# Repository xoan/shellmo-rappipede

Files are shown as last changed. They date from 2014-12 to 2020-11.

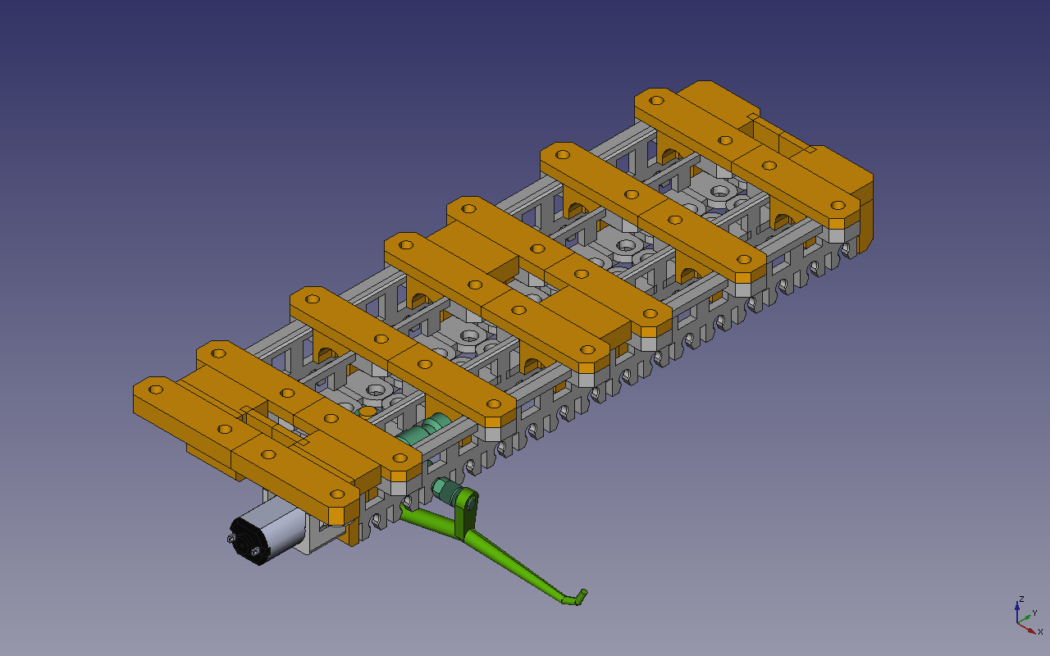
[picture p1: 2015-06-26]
images/chassis.png

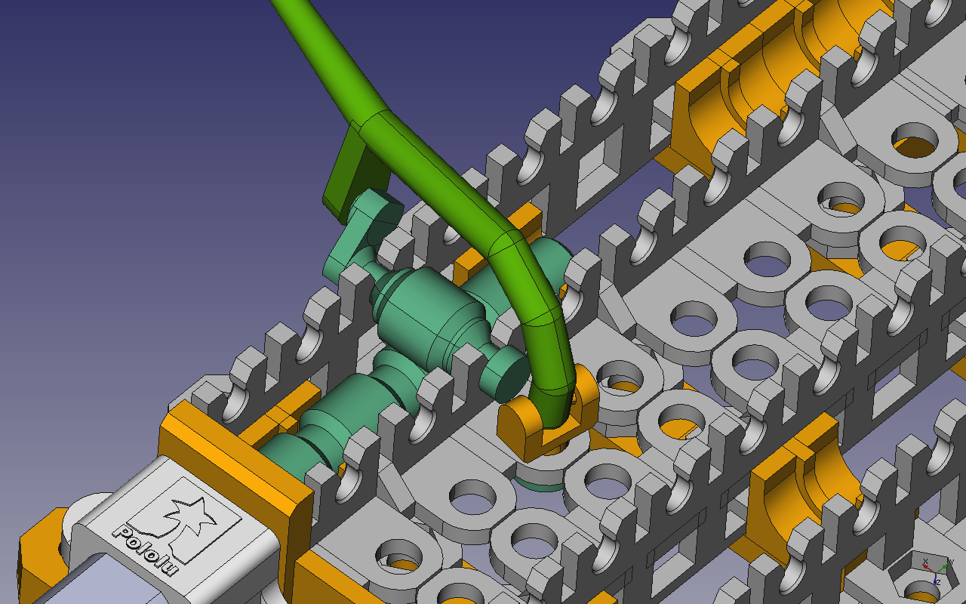
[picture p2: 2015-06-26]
images/leg-pin.png

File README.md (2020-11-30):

# Rappipede for Shellmo

RepRap printable version of [Micropede][mpdoc] motor module for [Shellmo][spweb].

[mpdoc]: http://shellmo.org/making-micropede.html
[spweb]: http://shellmo.org/

## Printing

All the parts can be printed without support.

Recommended settings for Slic3r 1.2.1:

* layer height: 0.25mm
* infill: 30%
* extrusion width: 0.5mm

## Assembly ([in pictures][mpagp])

* M3x8mm screw **x24**
* M3x10mm screw **x4** (for motor cover)
* M3 nut **x28**

Please, refer to `src/chassis.fcstd` to see the pin-leg connection and to
figure out how to assembly the whole thing. You must put all the pins before
to assembly the ribs, and also before this you must put the captive nuts.

Shaft is a tricky part. Try to fit all the shaft parts without glue and
without play, and insert in the ribs before put the rear one.

The rest is the same in [Micropede documentation][mpdoc].

The compatible motor cover is the one you can find in the [RepWalker][rwdoc].

[mpagp]: https://photos.app.goo.gl/5GXLVykhWVXsJaY36
[rwdoc]: http://shellmo.org/making-repwalker.html

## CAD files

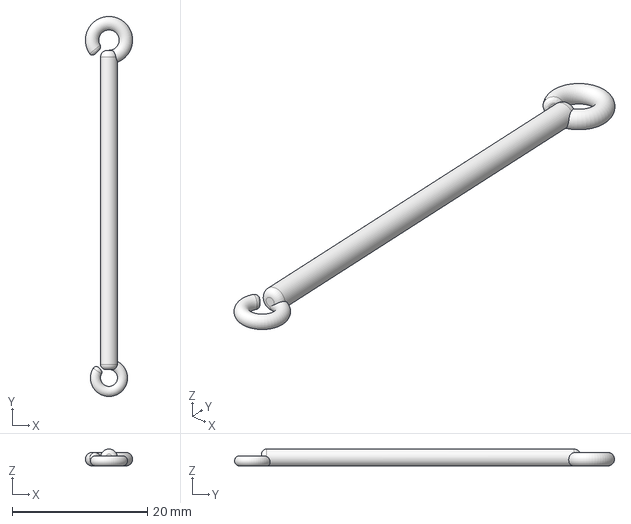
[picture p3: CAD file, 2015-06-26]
src/linkrod.fcstd
7.00 x 56.2 x 2.50 mm

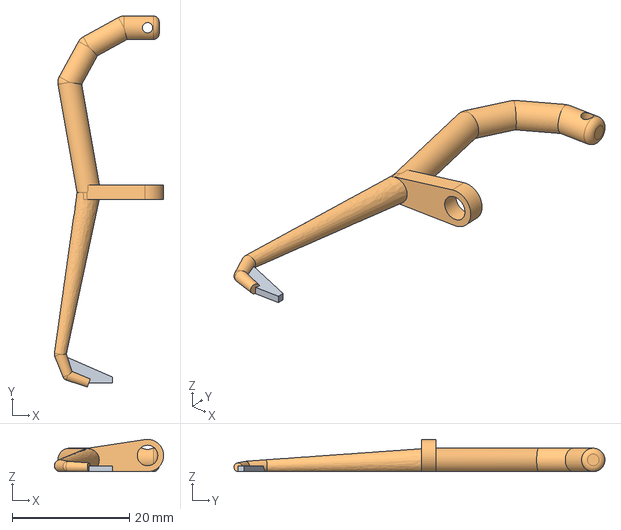
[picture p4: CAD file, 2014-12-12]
step/leg.step
18.6 x 63.2 x 5.50 mm

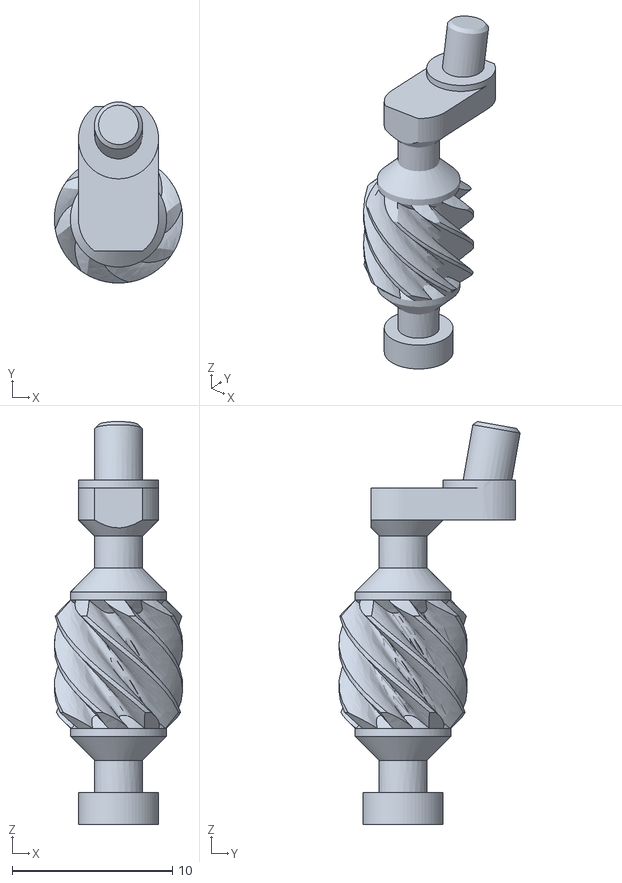
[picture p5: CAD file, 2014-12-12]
stl/ns/crank-RNS.stl
8.00 x 11.3 x 25.1

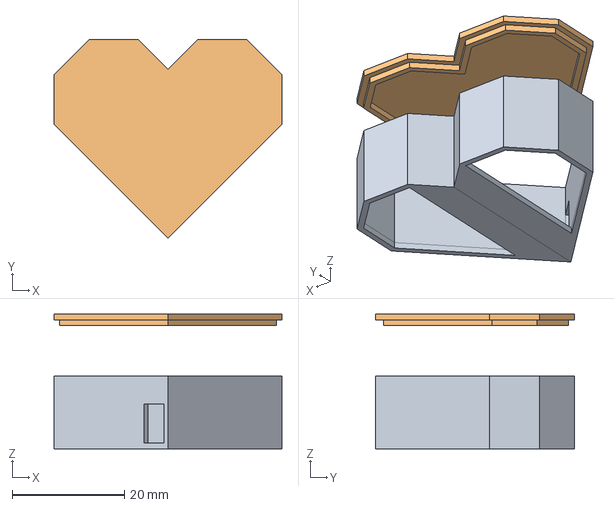
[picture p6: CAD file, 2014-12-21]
src/heart.fcstd
40.6 x 35.4 x 24.0 mm

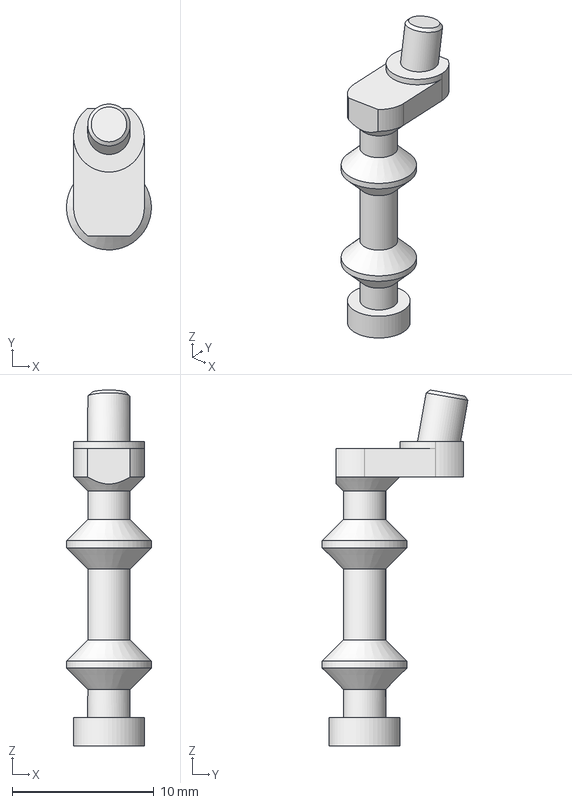
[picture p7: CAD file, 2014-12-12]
step/crank-axis.step
5.99 x 10.3 x 25.1 mm

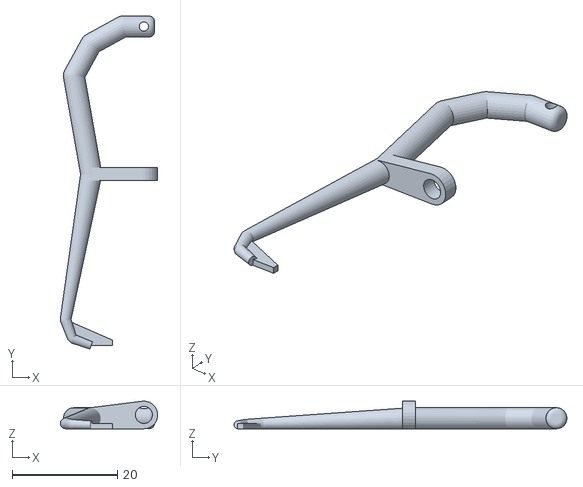
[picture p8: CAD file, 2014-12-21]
stl/leg-L_x16.stl
18.5 x 63.2 x 5.23

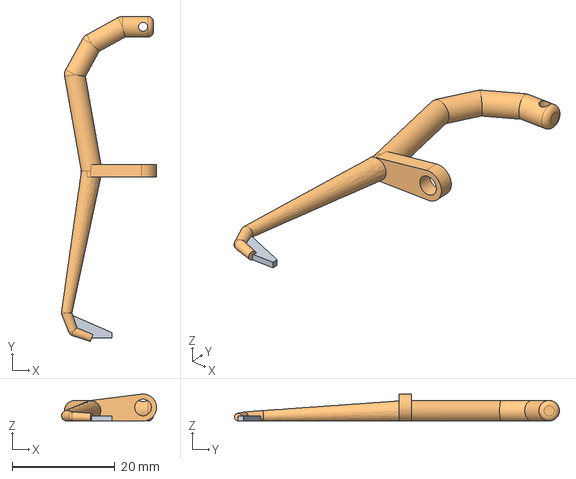
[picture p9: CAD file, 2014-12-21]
src/leg.fcstd
18.5 x 63.2 x 5.25 mm
foot-Pad001
leg-Fillet

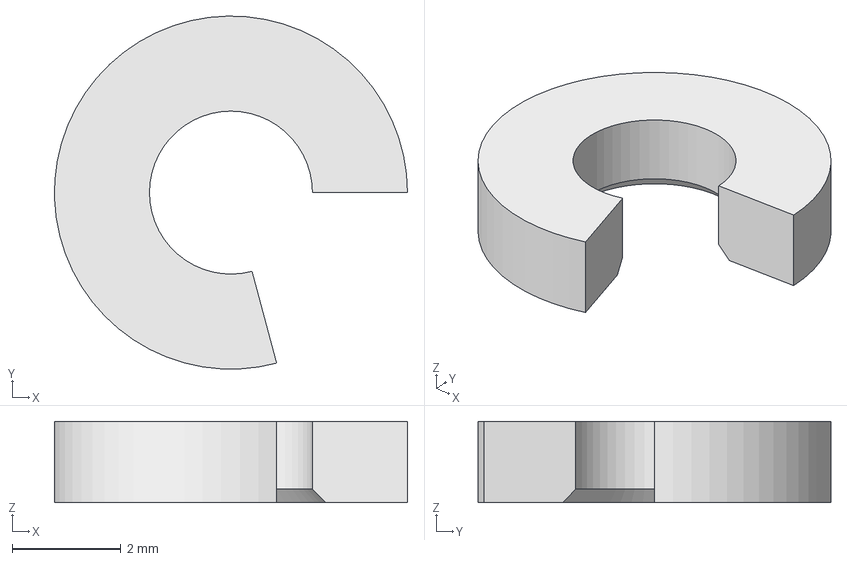
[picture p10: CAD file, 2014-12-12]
step/cring.step
6.50 x 6.50 x 1.50 mm

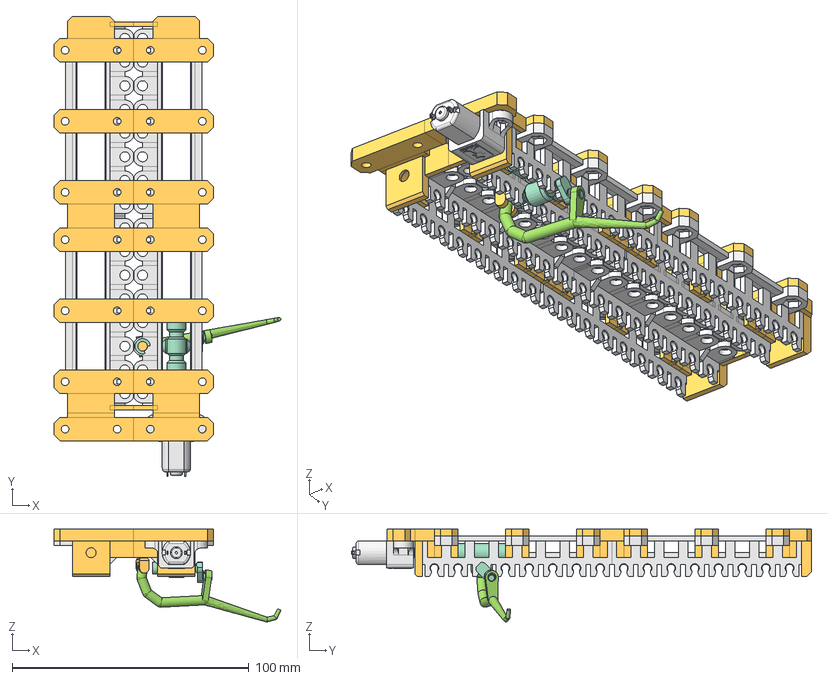
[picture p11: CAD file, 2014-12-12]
src/chasis.fcstd
95.8 x 194.2 x 39.2 mm
crank-Fusion-Clone009
shaft-Fusion009
motor-Part__Feature001
pin-Part__Feature002
leg-Part__Feature004
cring-Part__Feature005
outside-Compound
inside-Compound001
outside-Part__Mirroring004
inside-Part__Mirroring005
rib-Fusion019-Clone002
rib-Fusion019-Clone003
rib-union-Fusion021
rib-rear-Chamfer010
rib-front-Fusion025

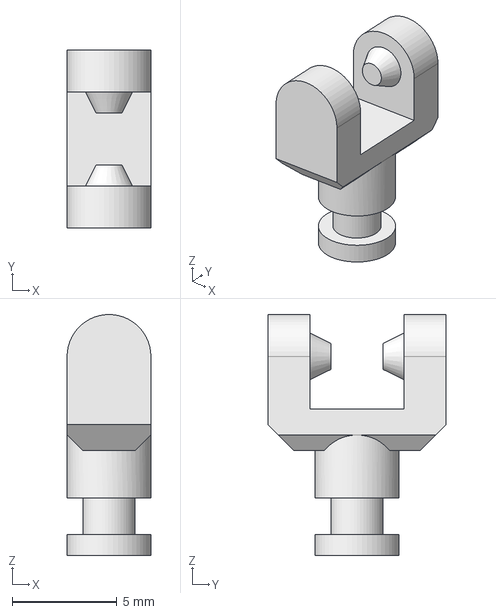
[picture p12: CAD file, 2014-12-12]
step/pin.step
4.00 x 8.50 x 11.5 mm

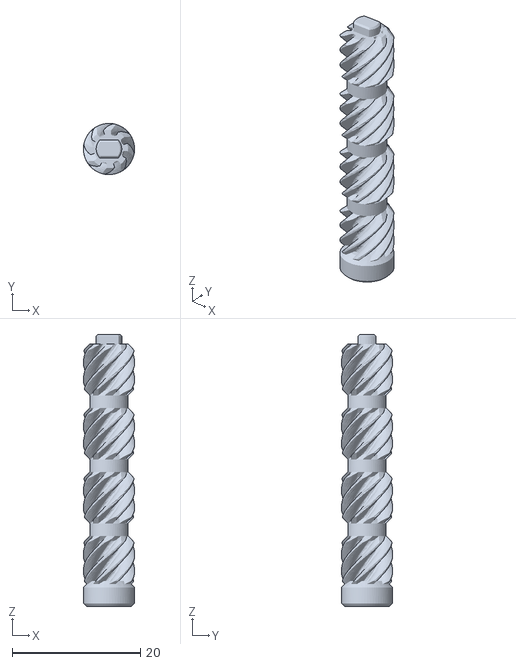
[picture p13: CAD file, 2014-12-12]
stl/shaft-FL_x1.stl
8.00 x 8.00 x 42.5

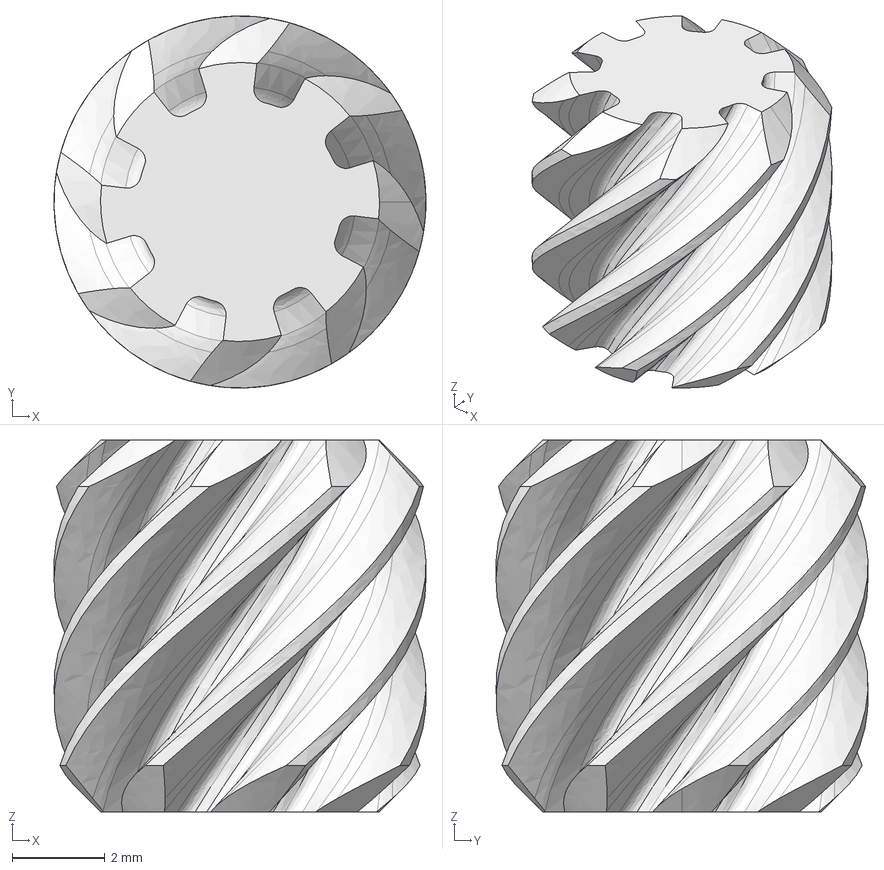
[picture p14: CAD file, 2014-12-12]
src/worm.fcstd
8.00 x 8.00 x 8.00 mm

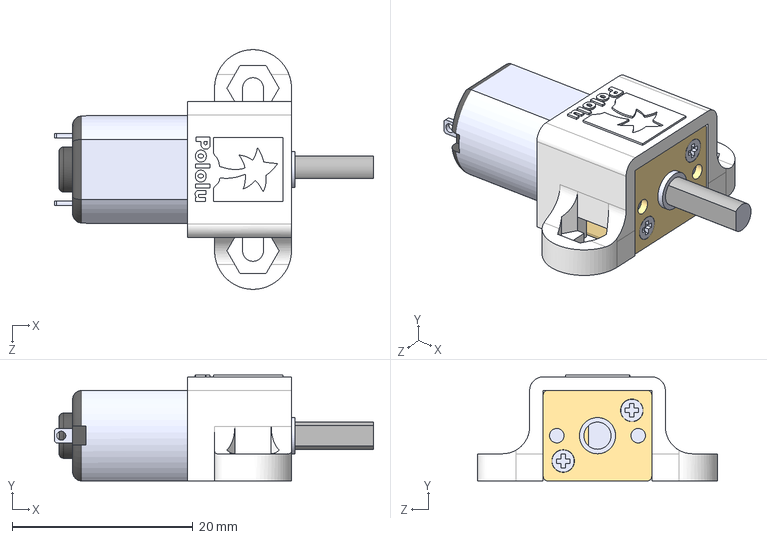
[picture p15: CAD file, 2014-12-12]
step/micro-metal-gearmotor-with-1086-bracket.step
35.3 x 11.7 x 26.5 mm

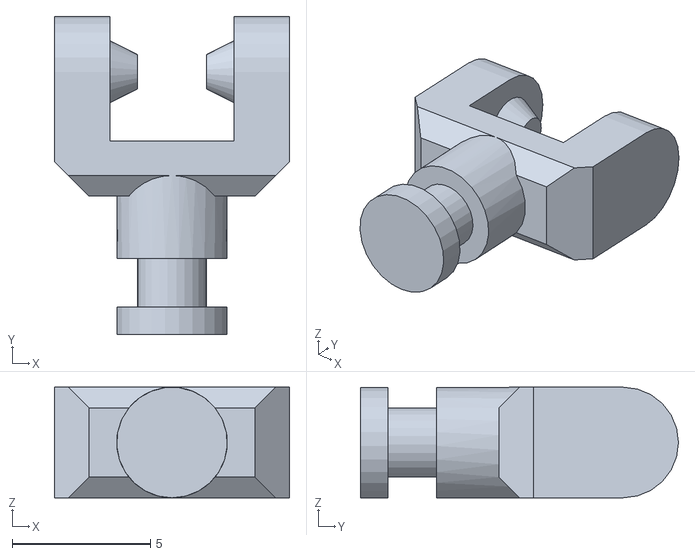
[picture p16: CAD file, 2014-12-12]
stl/pin_x32.stl
8.50 x 11.5 x 4.00

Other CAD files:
stl/linkrod_x8.stl
stl/ns/crank-LNS.stl
stl/leg-R_x16.stl
src/pin.fcstd
src/crank.fcstd
src/cring.fcstd
step/worm.step
stl/chassis-I_x4.stl
stl/chassis-O_x4.stl
stl/crank-L_x16.stl
stl/crank-R_x16.stl
stl/cring_x32.stl
stl/rib-F_x1.stl
stl/rib-M_x1.stl
stl/rib-R_x1.stl
stl/rib_x2.stl
stl/shaft-FR_x1.stl
stl/shaft-ML_x2.stl
stl/shaft-MR_x2.stl
stl/shaft-RL_x1.stl
stl/shaft-RR_x1.stl

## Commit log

2014-12-12 draft for assembly instructions
    [chasis.fcstd, crank-axis.step, cring.step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]
2014-12-21 adjust leg crank hole
    [leg-L_x16.stl, leg-R_x16.stl, leg.fcstd]
2014-12-21 update heart
    [heart.fcstd]
2015-04-16 Update README.md
    Link to assembly in pictures.
2015-06-26 added linkrod
    [linkrod.fcstd, linkrod_x8.stl]
